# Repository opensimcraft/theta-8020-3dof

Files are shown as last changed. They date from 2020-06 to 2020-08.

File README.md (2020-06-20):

# SC230 Theta 3DOF Sim Rig
The SC230 Theta is a 3DOF sim rig made from 80/20 T-slot aluminum extrusions and
other components.

## Assemblies
The SC230 Theta is made up of several chassis that come together to create
the whole rig. The rig may be expanded by starting with the inner-most
cockpit and adding additional chassis to add motion later on.

* Cockpit Chassis
* Pitch/Yaw Chassis
* Roll Chassis
* Cradle Chassis
  * Note: The Cradle Chassis is required to suspend the Roll Chassis

## TODOs
The primary activity right now is to finalize the Cockpit Chassis as a 1.0
release of the project by itself.

* Convert the single Word assembly instructions document into individual
  assembly instructions for each chassis
* Verify the 80/20 part numbers and machine codes to produce the BOMs for each
  chassis
* Convert the SKP to STEP for use with FreeCAD and break into files for each
  chassis

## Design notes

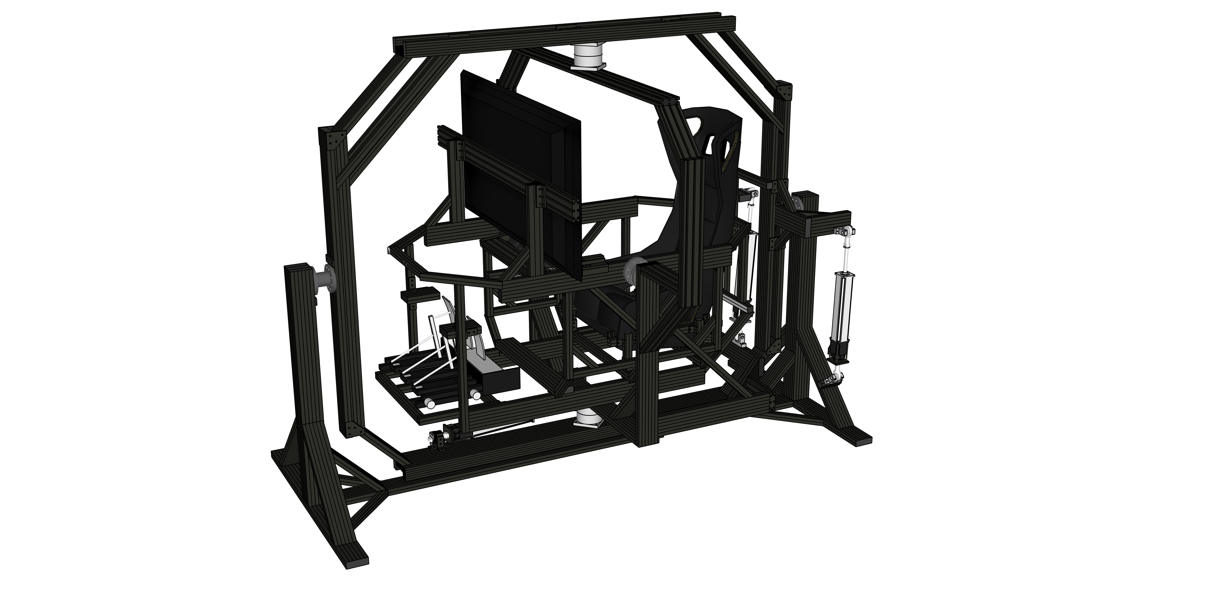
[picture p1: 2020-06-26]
SC230 Theta Large Screen.png

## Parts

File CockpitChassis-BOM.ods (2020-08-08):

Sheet: Export BOM
Open Sim Craft Part # | DIYSim Part # | Tag | Part # | Qty | Length Each (or area) | Units | 80/20 Description Note:all extrusion dimensions start at the left end
E9230301 | 9230301 | A | 1030-S | 2 | 38.25 | IN | 7036 Left; 7036 Right
 |  |  | 7003 | 2 |  | EA
 |  |  | 7036 | 2 |  | EA
E9230303 | 9230303 | B | 1010-S | 2 | 22 | IN | 7051 in S @ .500" Left; 7051 in S @ 1.500" Left; 7051 in S @ 2.500" Left, 7061 in Right
 |  |  | 7005 | 2 |  | EA
 |  |  | 7051 | 6 |  | EA
 |  |  | 7061 | 2 |  | EA
E9230906 | 9230906 | AB | 1010-S | 2 | 17 | IN | 7061 in Left; 7061 in Right, 7051 in S Left @ 2.250", 7051 in S Left @ 10.375"
 |  |  | 7005 | 2 |  | EA | 1
 |  |  | 7061 | 4 |  | EA | 1
 |  |  | 7051 | 4 |  | EA | 1
 |  |  | 7005 | 2 |  | EA | 1
 |  |  | 7051 | 6 |  | EA | 1
 |  |  | 7061 | 2 |  | EA | 1
E9230309 | 9230309 | C | 1010-S | 2 | 21.75 | IN | 7061 in Left; 7061 in Right
 |  |  | 7005 | 2 |  | EA | 1
 |  |  | 7061 | 4 |  | EA | 1
E9230310 | 9230310 | D | 1010-S | 2 | 10.85 | IN | 7061 in Left and Right, 7051 in S @ 0.500
 |  |  | 7005 | 2 |  | EA | 1
 |  |  | 7061 | 4 |  | EA | 1
 |  |  | 7051 | 2 |  | EA | 1
E9230312 | 9230312 | E | 1010-S | 2 | 19 | IN | 1010-S
 |  |  | 7005 | 2 |  | EA | 1
E9230313 | 9230313 | F | 1010-S | 6 | 13 | IN | 7042 in C Left; 7042 in A Left; 7061 in Right, 7051 in A Right @ 0.5"
 |  |  | 7005 | 6 |  | EA | 1
 |  |  | 7042 | 12 |  | EA | 1
 |  |  | 7061 | 6 |  | EA | 1
 |  |  | 7051 | 6 |  | EA | 1
E9230314 | 9230314 | G | 1010-S | 2 | 11 | IN | 7061 in Left; 7061 in Right, 7051 in S @ 0.500"
 |  |  | 7005 | 2 |  | EA | 1
 |  |  | 7061 | 4 |  | EA | 1
 |  |  | 7051 | 2 |  | EA | 1
E9230315 | 9230315 | H | 1010-S | 1 | 13 | IN | 1010-S
 |  |  | 7005 | 1 |  | EA | 1
E9230316 | 9230316 | I | 1020-S | 1 | 6.5 | IN | 1020-S
 |  |  | 7000 | 1 |  | EA | 1
E9230317 | 9230317 | J | 1010-S | 1 | 15 | IN | 7051 in S @ 7.000"; 7051 in S @ 8.000"
 |  |  | 7005 | 1 |  | EA | 1
 |  |  | 7051 | 2 |  | EA | 1
E9230318 | 9230318 | K | 1030-S | 2 | 36 | IN | 7036 Left; 7036 Right, 7050 in U @ 1.000" (U Channel adjacent to taps)
 |  |  | 7003 | 2 |  | EA | 1
 |  |  | 7036 | 4 |  | EA | 1
 |  |  | 7050 | 2 |  | EA | 1
E9230323 | 9230323 | L | 1010-S | 2 | 12 | IN | 7081; 7050 in slot R at 2.0" from Left End
 |  |  | 7005 | 2 |  | EA | 1
 |  |  | 7081 | 2 |  | EA | 1
 |  |  | 7050 | 2 |  | EA | 1
E9230324 | 9230323 | M | 1010-S | 2 | 12 | IN | 7081; 7050 in slot R at 5.0" from Left End
 |  |  | 7005 | 2 |  | EA | 1
 |  |  | 7081 | 2 |  | EA | 1
 |  |  | 7050 | 2 |  | EA | 1
E9230325 | 9230325 | N | 1010-S | 1 | 13 | IN | 7061 in Left; 7061 in Right; 7051 in S @ 2.000"; 7051 in S @ 3.000"; 7051 in S @ 10.000" ; 7051 in S @ 11.000" from left, 7253 in S @ 6.000"; 7253 in S @ 7.000" from left
 |  |  | 7005 | 1 |  | EA | 1
 |  |  | 7061 | 2 |  | EA | 1
 |  |  | 7051 | 4 |  | EA | 1
 |  |  | 7253 | 2 |  | EA | 1
E9230326 | 9230326 | O | 1030-S | 2 | 12 | IN | 7036 Left; 7036 Right
 |  |  | 7003 | 2 |  | EA | 1
 |  |  | 7036 | 4 |  | EA | 1
E9230327 | 9230327 | P | 1010-S | 1 | 22 | IN | 7051 in S @ 10.000"; 7051 in S @ 11.000"; 7051 in S @ 12.000"
 |  |  | 7005 | 1 |  | EA | 1
 |  |  | 7051 | 3 |  | EA | 1
E9230331 | 9230331 | Q | 1010-S | 2 | 5 | IN | 7051 in S @ 2.000";7051 in S @ 3.000"; 7051 in S @ 4.000"
 |  |  | 7005 | 2 |  | EA | 1
 |  |  | 7051 | 6 |  | EA | 1
E9230332 | 9230332 | R | 1010-S | 1 | 21 | IN | 7051 in S @ 2.500"; 7051 in R @ 9.500"; 7051 in R @ 10.500"; 7051 in R @ 11.500", 7051 in S @ 18.500"
 |  |  | 7005 | 1 |  | EA | 1
 |  |  | 7051 | 5 |  | EA | 1
E9230333 | 9230333 | S | 1010-S | 1 | 13 | IN | 7061 in Left; 7061 in Right, 7253 in S @ 5.500";7253 in S @ 6.500"; 7253 in S @7.500" from left
 |  |  | 7005 | 1 |  | EA | 1
 |  |  | 7061 | 2 |  | EA | 1
 |  |  | 7253 | 3 |  | EA | 1
E9230334 | 9230334 | T | 1030-S | 2 | 23 | IN | 7036 in Left; 7036 in Right
 |  |  | 7003 | 2 |  | EA | 1
 |  |  | 7036 | 4 |  | EA | 1
E9230335 | 9230335 | U | 1010-S | 2 | 8 | IN | 7051 in R Left @ 0.5"; 7051 in R Left @ 1.5";7051 in R Left @ 2.5";7051 in R Left @ 7.5"; 7051 in R Left @ 6.5"; 7051 in R Left @ 5.5"
 |  |  | 7005 | 2 |  | EA | 1
 |  |  | 7051 | 12 |  | EA | 1
E9230336 | 9230336 | V | 1020-S | 4 | 4 | IN | 1020-S
 |  |  | 7000 | 4 |  | EA | 1
E9230337 | 9230337 | W | 1030-S | 2 | 9.5 | IN | 7036 in Left; 7086 Right
 |  |  | 7003 | 2 |  | EA | 1
 |  |  | 7036 | 2 |  | EA | 1
 |  |  | 7086 | 2 |  | EA | 1
E9230338 | 9230338 | X | 1030-S | 2 | 18.5 | IN | 7086 Right
 |  |  | 7003 | 2 |  | EA | 1
 |  |  | 7086 | 2 |  | EA | 1
E9230339 | 9230339 | Y | 1030-S | 1 | 48 | IN | 7051 in V Left @ 0.5"; 7051 in VV Left @ 0.5"; 7051 in U Left @ 0.5"; 7051 in V Right @ 0.5"; 7051 in VV Right @ 0.5"; 7051 in U Right @ 0.5";
 |  |  | 7003 | 1 |  | EA | 1
 |  |  | 7051 | 6 |  | EA | 1
E9230340 | 9230340 | Z | 1020-S | 2 | 15 | IN | 7042 in E Left; 7042 in H Left; 7051 in T Right @ 0.5"; 7051 in T Right @ 1.5"
 |  |  | 7000 | 2 |  | EA | 1
 |  |  | 7042 | 4 |  | EA | 1
 |  |  | 7051 | 4 |  | EA | 1
E9230341 | 9230341 | AA | 1020-S | 2 | 11 | IN | 1020-S
 |  |  | 7000 | 2 |  | EA | 1
E9230906 | 9230906 | AB | 1010-S | 2 | 17 | IN | 7061 in Left; 7061 in Right, 7051 in S Left @ 2.250", 7051 in S Left @ 10.375"
 |  |  | 7005 | 2 |  | EA | 1
 |  |  | 7061 | 4 |  | EA | 1
 |  |  | 7051 | 4 |  | EA | 1
E9230907 | 9230907 | AC | 1010-S | 2 | 10 | IN | 7061 in Left; 7061 in Right, 7051 in S @ 4.250"
 |  |  | 7005 | 2 |  | EA | 1
 |  |  | 7061 | 4 |  |  | 1
 |  |  | 7051 | 2 |  |  | 1
E9230908 | 9230908 | AD | 1010-S | 2 | 12 | IN | 7061 in Left, 7051 in S @ .500", 7051 in S @ 11.500"
 |  |  | 7005 | 2 |  | EA | 1
 |  |  | 7061 | 2 |  | EA | 1
 |  |  | 7051 | 4 |  | EA | 1
E9230909 | 9230909 | AE | 1020-S | 2 | 5 | IN | 1020-S
 |  |  | 7005 | 2 |  | EA | 1
E9232565 | 9232565 | AF | 2565 | 14 |  | EA | 1
E9232570 | 9232570 | AG | 2570 | 8 |  | EA | 1
F9236850 | 9236850 | AH | 6850 | 2 |  | EA | 1
E9230319 | 9230309F | AI | 1030-S | 1 | 21.75 | IN | 7061 in Left; 7061 in Right, one hole on each side, same channel
 |  |  | 7003 | 1 |  | EA | 1
 |  |  | 7061 | 2 |  | EA | 1
E9230320 | 9230311a | AJ | 1010-S | 4 | 6 | IN | 7066 @ 45 degrees in Left w/ 7083 Counterbore
 |  |  | 7005 | 4 |  | EA | 1
 |  |  | 7066 | 4 |  | EA | 1
 |  |  | 7083 | 4 |  | EA | 1
E9230321 | 9230311b | AK | 1010-S | 4 | 6 | IN | 1010-S
 |  |  | 7005 | 4 |  | EA | 1
E9230322 | 9230314B | AL | 1010-S | 2 | 11 | IN | 7042 in C Left; 7042 in A Left; 7061 in Right
 |  |  | 7005 | 2 |  | EA | 1
 |  |  | 7042 | 4 |  | EA | 1
 |  |  | 7061 | 2 |  | EA | 1
F9234119 | 9234119 | AM | 4119 | 34 |  | EA | 10 Series 2 Hole - Inside Corner Bracket
F9234176 | 9234176 | AN | 4176 | 16 |  | EA | 10 Series 3 Hole - Inside Corner Bracket
F9234136 | 9234136 | AO | 4136 | 2 |  | EA | 10 Series 4 Hole - Tall Gusseted Inside Corner Bracket
F9234015 | 9234015 | AP | 4015 | 11 |  | EA | 10 Series 6 Hole - Wide 3x3 Inside Corner Bracket
F9234166 | 9234166 | AQ | 4166 | 4 |  | EA | 10 Series 6 Hole - Rectangular Flat Plate
F9234118 | 9234118 | AR | 4118 | 8 |  | EA | 10 Series 3 Hole - Straight Flat Plate
F9234107 | 9234107 | AS | 4107 | 2 |  | EA | 10 Series 2 Hole - Straight Flat Plate
F9233393 | 9233393 |  | 3393 | 200 |  | EA | Bolt Assembly: 1/4-20 x .500" Black BHSCS and Slide-In Economy T-Nut - Centered Thread - Black Zinc
F9233381 | 9233381 |  | 3381 | 36 |  | EA | Standard End Fastener, 1/4-20
F9233395 | 9233395 |  | 3395 | 20 |  | EA | 10 Series 10-32 Standard Anchor Fastener Assembly
F9234503 | 9234503 | AT | 4503 | 4 |  | EA | 10 to 15 Series 2 Hole - Transition Inside Corner Bracket
F9233321 | 9233321 |  | 3321 | 24 |  | EA | Bolt Assembly: 1/4-20 x .500" Black FBHSCS and Slide-In Economy T-Nut - Centered Thread - Black Zinc
F9233305 | 9233305 |  | 3305 | 16 |  | EA | Bolt Assembly: 1/4-20 x .875" Black SHCS and Slide-In Economy T-Nut - Centered Thread - Black Zinc
F9233307 | 9233307 |  | 3307 | 12 |  | EA | Bolt Assembly: 1/4-20 x 1.250" Black SHCS and Slide-In Economy T-Nut - Centered Thread - Black Zinc
F9233065 | 9233065 |  | 3065 | 12 |  | EA | 1/4-20 x .750" Button Head Socket Cap Screw (BHSCS)
F9233080 | 9233080 |  | 3080 | 12 |  | EA | 1/4-20 x 1.500" Socket Head Cap Screw (SHCS)
F9233258 | 9233258 |  | 3258 | 100 |  | EA | .286" ID Washer
F9233376 | 9233376 |  | 3376 | 24 |  | EA | 1/4-20 Roll-In T-Nut with Flex Handle
F9233416 | 9233416 |  | 3059 | 12 |  | EA | 1/4-20 x .375" Button Head Socket Cap Screw (BHSCS)
F9233416 | 9233416 |  | 3382 | 12 |  | EA | 1/4-20 Slide-in Economy T-Nut - Centered Thread
F9233822 | 9233822 |  | 3497 | 12 |  | EA | Bolt Assembly: 1/4-20 x .625" Black SHCS with Washer and Slide-In Economy T-Nut - Centered Thread - Black Zinc
F9233822 | 9233822 |  | 3497 | 24 |  | EA | Bolt Assembly: 1/4-20 x .625" Black SHCS with Washer and Slide-In Economy T-Nut - Centered Thread - Black Zinc
F9236416 | 9236416 | AU | 6416 | 2 |  | EA | 10 S 4" SINGLE FLANGE BEARINGBRAKE KIT READY
F9236540 | 9236540 |  | 11-6540 | 4 |  | EA | M6 X 40mm SHCS [BLACK]

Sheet: Bottom Mount Pedal Frame
Open Sim Craft Part # | DIYSim Part # | Tag | Part # | Qty | Length Each (or area) | Units | 80/20 Description Note:all extrusion dimensions start at the left end
E9230906 | 9230906 | AB | 1010-S | 2 | 17 | IN | 7061 in Left; 7061 in Right, 7051 in S Left @ 2.250", 7051 in S Left @ 10.375"
 |  |  | 7005 | 2 |  | EA | 1
 |  |  | 7061 | 4 |  | EA | 1
 |  |  | 7051 | 4 |  | EA | 1
F9233381 | 9233381 |  | 3381 | 8 |  | EA | Standard End Fastener, 1/4-20
E9230907 | 9230907 | AC | 1010-S | 2 | 10 | IN | 7061 in Left; 7061 in Right, 7051 in S @ 4.250"
 |  |  | 7005 | 2 |  | EA | 1
 |  |  | 7061 | 4 |  |  | 1
 |  |  | 7051 | 2 |  |  | 1
E9230908 | 9230908 | AD | 1010-S | 2 | 12 | IN | 7061 in Left, 7051 in S @ .500", 7051 in S @ 11.500"
 |  |  | 7005 | 2 |  | EA | 1
 |  |  | 7061 | 2 |  | EA | 1
 |  |  | 7051 | 4 |  | EA | 1

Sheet: Bottom Cockpit
Open Sim Craft Part # | DIYSim Part # | Tag | Part # | Qty | Length Each (or area) | Units | 80/20 Description Note:all extrusion dimensions start at the left end
E9230301 | 9230301 | A | 1030-S | 2 | 38.25 | IN | 7036 Left; 7036 Right
 |  |  | 7003 | 2 |  | EA
 |  |  | 7036 | 2 |  | EA
E9230303 | 9230303 | B | 1010-S | 2 | 22 | IN | 7051 in S @ .500" Left; 7051 in S @ 1.500" Left; 7051 in S @ 2.500" Left, 7061 in Right
 |  |  | 7005 | 2 |  | EA
 |  |  | 7051 | 6 |  | EA
 |  |  | 7061 | 2 |  | EA
F9234119 | 9234119 | AM | 4119 | 4 |  | EA | 10 Series 2 Hole - Inside Corner Bracket
F9234015 | 9234015 | AP | 4015 | 2 |  | EA | 10 Series 6 Hole - Wide 3x3 Inside Corner Bracket
E9230309 | 9230309 | C | 1010-S | 2 | 21.75 | IN | 7061 in Left; 7061 in Right
 |  |  | 7005 | 2 |  | EA
 |  |  | 7061 | 4 |  | EA
E9230319 | 9230309F | AI | 1030-S | 1 | 21.75 | IN | 7061 in Left; 7061 in Right, one hole on each side, same channel
 |  |  | 7003 | 1 |  | EA
 |  |  | 7061 | 2 |  | EA
E9232565 | 9232565 | AF | 2565 | 6 |  | EA

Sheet: Rear Cockpit
Open Sim Craft Part # | DIYSim Part # | Tag | Part # | Qty | Length Each (or area) | Units | 80/20 Description Note:all extrusion dimensions start at the left end
E9230332 | 9230332 | R | 1010-S | 1 | 21 | IN | 7051 in S @ 2.500"; 7051 in R @ 9.500"; 7051 in R @ 10.500"; 7051 in R @ 11.500", 7051 in S @ 18.500"
 |  |  | 7005 | 1 |  | EA
 |  |  | 7051 | 5 |  | EA
E9232570 | 9232570 | AG | 2570 | 2 |  | EA
E9230310 | 9230310 | D | 1010-S | 2 | 10.85 | IN | 7061 in Left and Right, 7051 in S @ 0.500
 |  |  | 7005 | 2 |  | EA
 |  |  | 7061 | 4 |  | EA
 |  |  | 7051 | 2 |  | EA

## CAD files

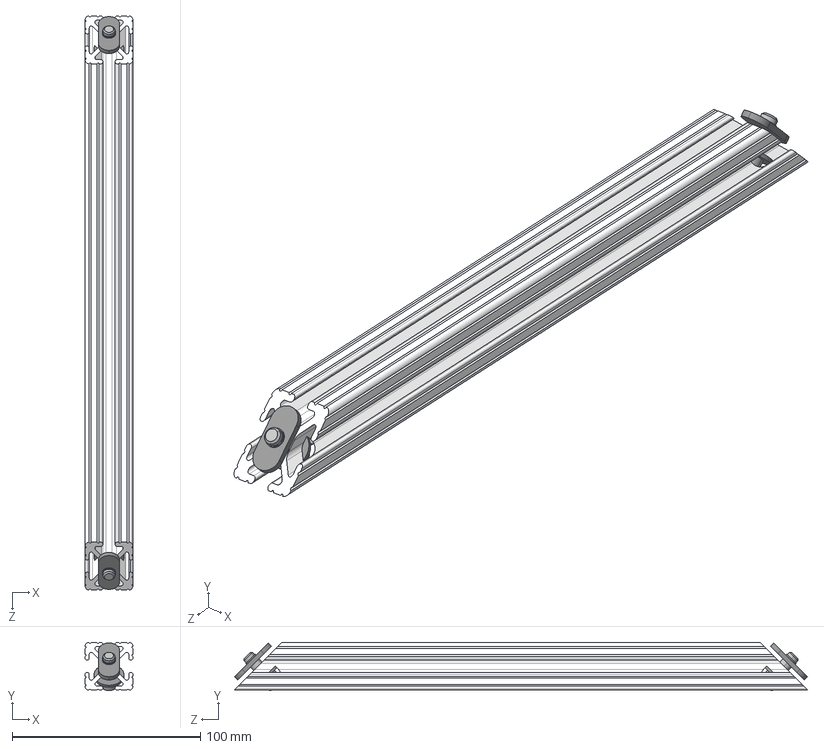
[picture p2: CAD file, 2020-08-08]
8020-stepfiles/8020-2570.STEP
25.4 x 25.6 x 304.8 mm
1010-12in
socket head cap screw_ai_HX-SHCS 0.25-20x0.625x0.625-N x 2

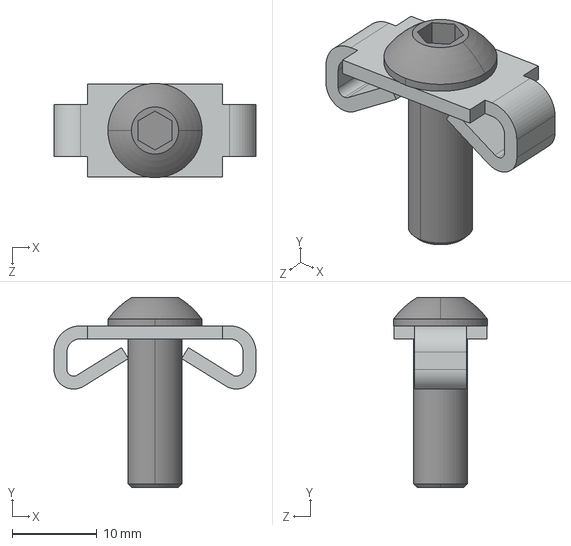
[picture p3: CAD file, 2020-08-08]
8020-stepfiles/8020-3381.STEP
23.8 x 22.4 x 11.1 mm
8020-3381-$PARTNUMBER_3378
8020-3381-$PARTNUMBER_3065

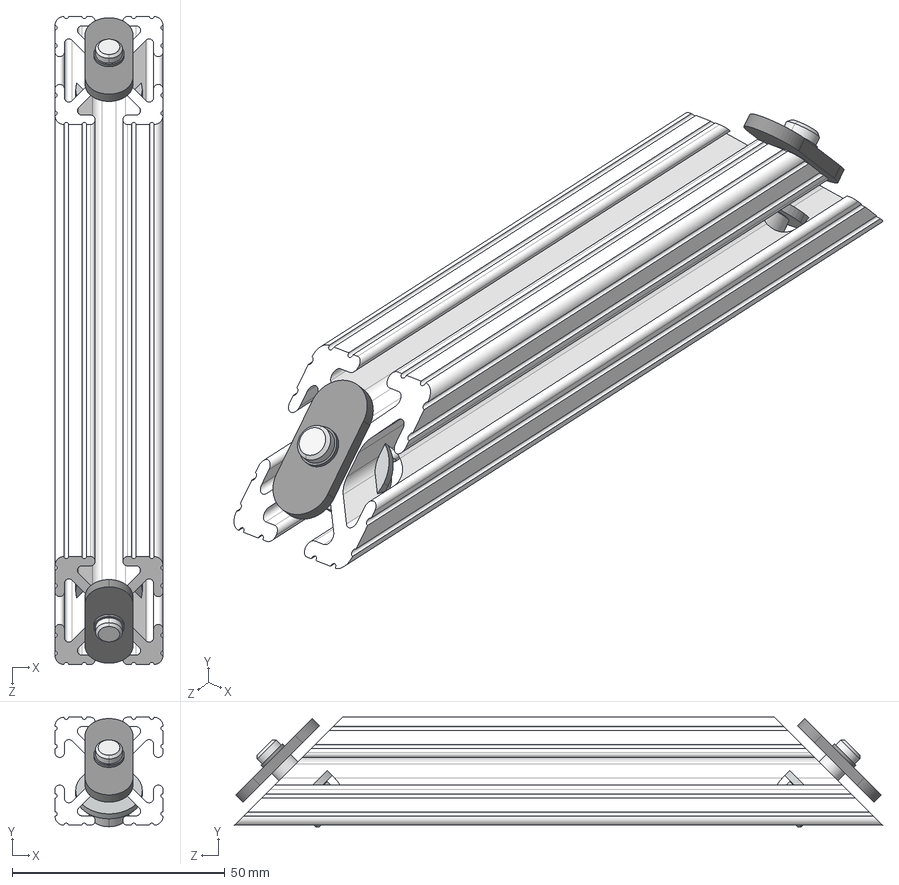
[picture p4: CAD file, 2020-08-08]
8020-stepfiles/8020-2565.STEP
25.4 x 25.8 x 152.4 mm
3258_Preferred Wide FW 0.25 x 2

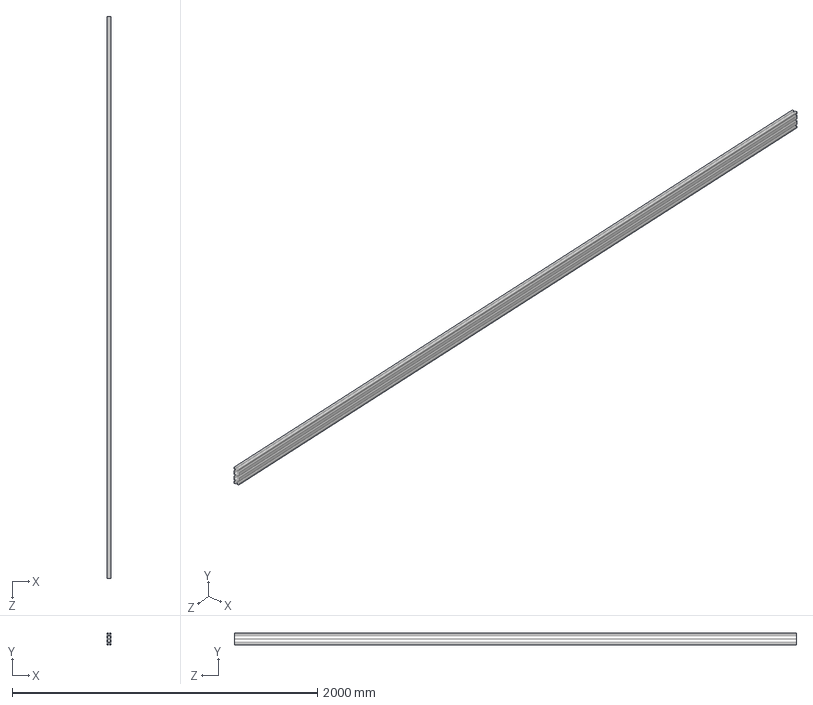
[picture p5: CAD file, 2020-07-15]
8020-stepfiles/8020-1030-S X 145.step
25.4 x 76.2 x 3683.0 mm

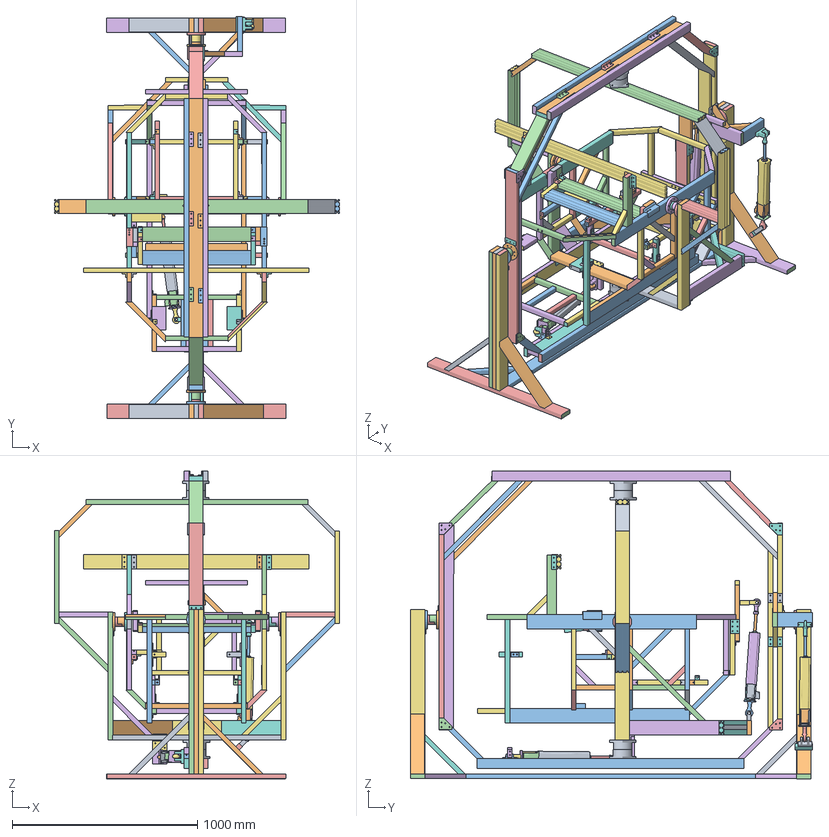
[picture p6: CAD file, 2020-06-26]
sc230_theta_large_screen-from-dae.FCStd
1539.5 x 2171.3 x 1661.5 mm

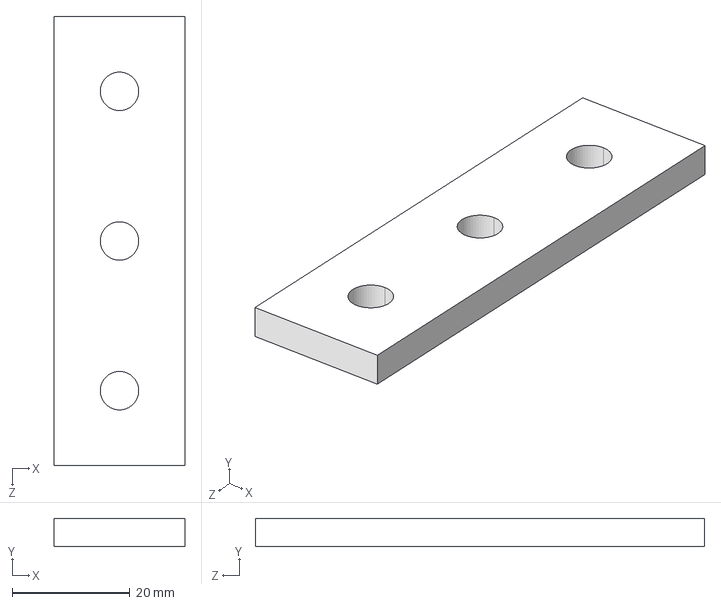
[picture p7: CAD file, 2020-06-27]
8020-stepfiles/8020-4118.step
22.2 x 4.78 x 76.2 mm

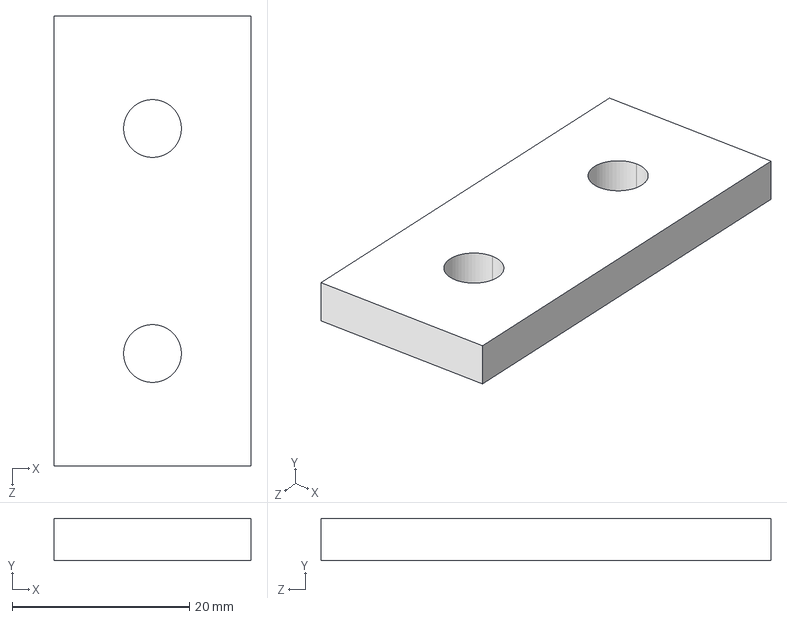
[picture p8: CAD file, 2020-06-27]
8020-stepfiles/8020-4107.step
22.2 x 4.78 x 50.8 mm

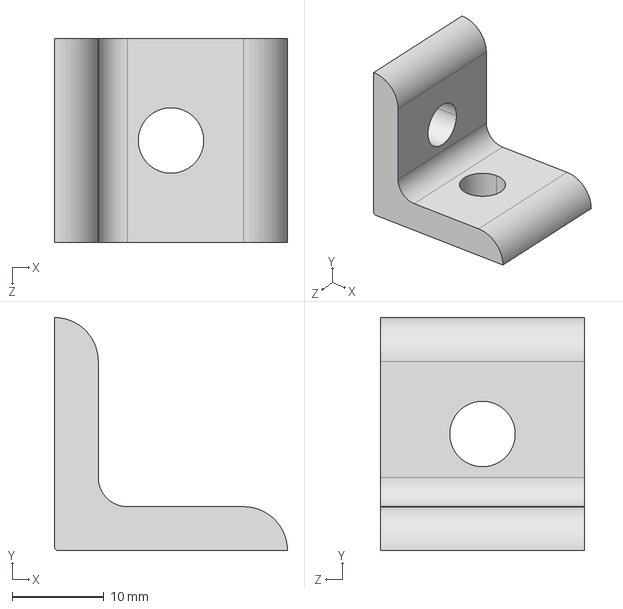
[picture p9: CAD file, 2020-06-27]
8020-stepfiles/8020-4119.step
25.4 x 25.4 x 22.2 mm

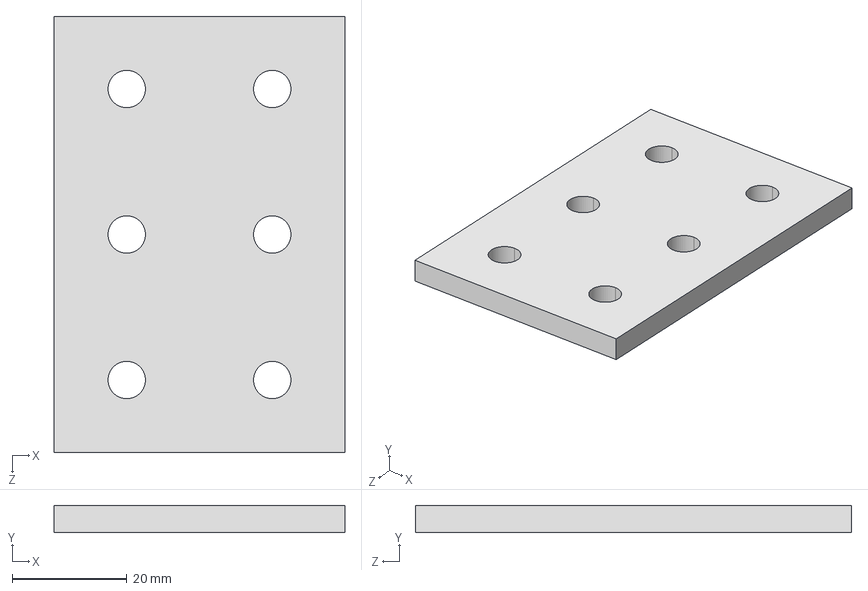
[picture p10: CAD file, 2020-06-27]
8020-stepfiles/8020-4166.step
50.8 x 4.78 x 76.2 mm

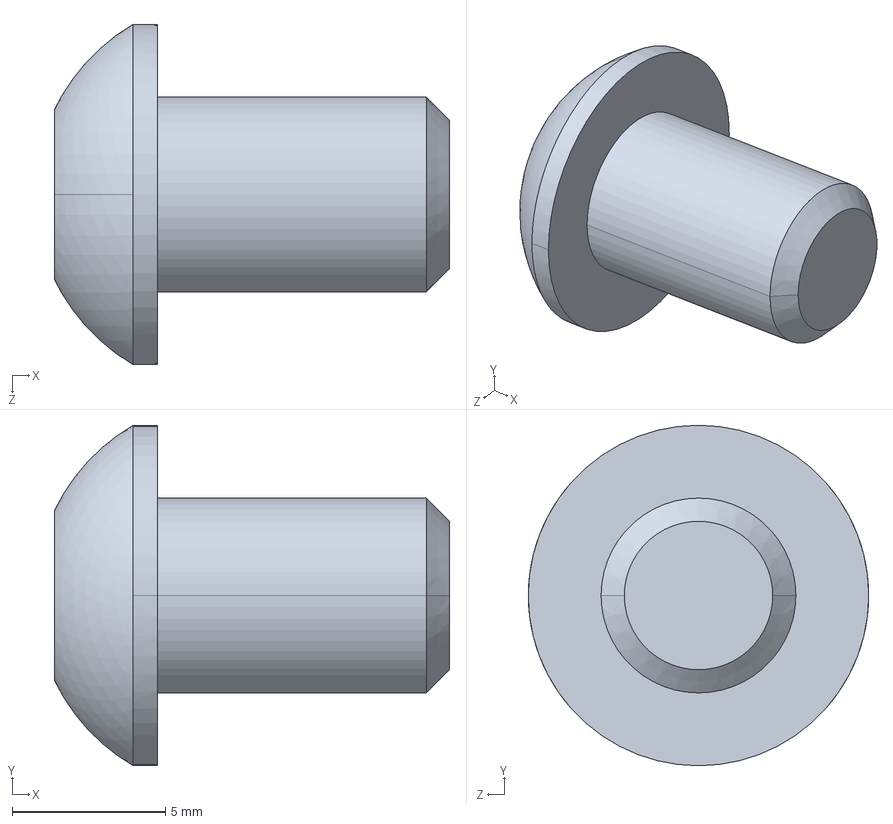
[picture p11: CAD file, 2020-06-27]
8020-stepfiles/8020-3059.step
12.9 x 11.1 x 11.1 mm

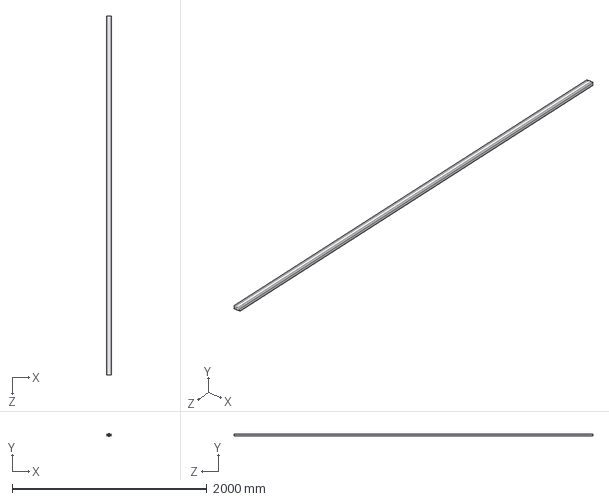
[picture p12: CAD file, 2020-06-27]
8020-stepfiles/8020-1020-S X 145.step
50.8 x 25.4 x 3683.0 mm

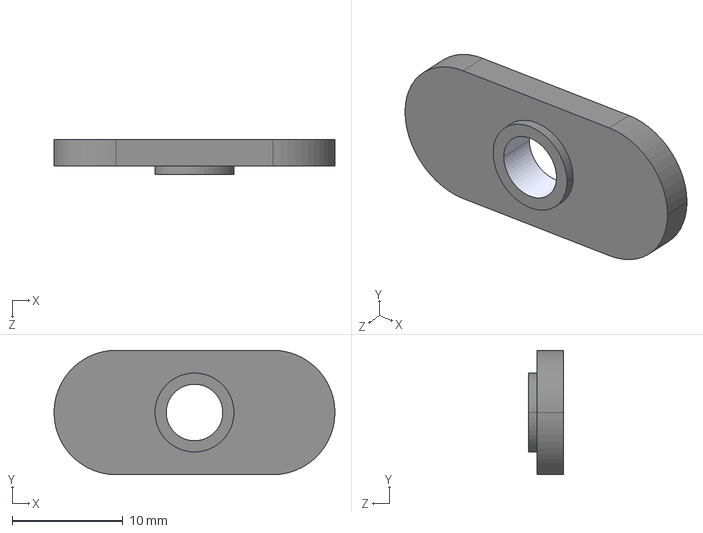
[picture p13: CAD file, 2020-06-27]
8020-stepfiles/8020-3382.step
25.4 x 11.3 x 3.17 mm

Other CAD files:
bottom-mount-pedal-frame/Subassembly_Bottom_Mount_Pedal_Frame.FCStd
cockpit-rear/Subassembly_Cockpit_Rear.FCStd
cockpit-bottom/Subassembly_Cockpit_Bottom.FCStd
extrusion-profile-1010-S.FCStd
extrusion-profile-1020-S.FCStd
extrusion-profile-1030-S.FCStd
8020-stepfiles/8020-1010-S X 145.step
8020-stepfiles/8020-3065.step
8020-stepfiles/8020-3080.step
8020-stepfiles/8020-3258.step
8020-stepfiles/8020-4015.step
8020-stepfiles/8020-4136.step
8020-stepfiles/8020-4176.step
8020-stepfiles/8020-4503.step
bottom-mount-pedal-frame/E9230906.FCStd
bottom-mount-pedal-frame/E9230907.FCStd
bottom-mount-pedal-frame/E9230908.FCStd
cockpit-bottom/E9230301.FCStd
cockpit-bottom/E9230303.FCStd
cockpit-bottom/E9230309.FCStd
cockpit-bottom/E9230319.FCStd
cockpit-bottom/E9232565.FCStd
cockpit-rear/E9230310.FCStd
cockpit-rear/E9230332.FCStd
cockpit-rear/E9232570.FCStd
fasteners-brackets-etc/F9234015.FCStd
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

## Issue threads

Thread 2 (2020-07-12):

machine codes in bottom mount pedal assembly need to be rectified

thoraxe, 2020-07-12:
Looking at the sample equipment I received from SimCraft, it appears that the machine codes for 9230906 are not entirely correct.

> There are 3-7051. The one at 2.250”, the one at 10.375”, but also one at 6.375”. This doesn’t match the CAD in terms of the spacing between the components.

This is also added as a comment on the BOM tab where the pedal mount assembly appears.

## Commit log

2020-06-20 adds distinct cockpit chassis documentation
2020-06-23 Add files via upload
    Stepfile Added
    [sc230_LargeScreen v1.step]
2020-06-26 adds freecad file
    [sc230_theta_large_screen.FCStd]
2020-06-26 removes empty step file
    [sc230_LargeScreen v1.step]
2020-06-27 adds step files for various 8020 components
    [8020-1010-S X 145.step, 8020-1020-S X 145.step, 8020-3059.step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]
2020-06-29 adds BOM spreadsheet for cockpit chassis
    [CockpitChassis-BOM.ods]
2020-07-11 Adds a sheet for the bottom pedal frame
    This adds a sheet which has a BOM specific for the bottom pedal frame. We may
    or may not make multiple sheets for each of the sub-assemblies that go into the
    main assemblies.
    [CockpitChassis-BOM.ods]
2020-07-11 Adds bottom mount pedal frame files
    [9230906.FCStd, 9230907.FCStd, 9230908.FCStd]
2020-07-12 Adds assembly files for Assembly4
    This creates individual assemblies from the previously added parts and then
    creates a parent assembly for the bottom frame.
    [9230906-assy.FCStd, 9230907-assy.FCStd, 9230908-assy.FCStd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]
2020-07-12 adds BOM comment about discrepancy in machine codes
    [CockpitChassis-BOM.ods]
2020-07-15 adds remaining extrusions to bottom mount pedal frame assembly
    [9230908-assy.FCStd, bottom-mount-pedal-frame-assy.FCStd]
2020-07-15 adds 1030-s step file
    [8020-1030-S X 145.step]
2020-07-15 Starts to work on base cockpit
    * This adds a simple extrusion profile from which to make other 1010-S parts.
    * It adds a folder to store converted parts/assemblies for fasteners, brackets,
    etc.
    * It adds the starting parts for the base cockpit frame
    [1010-S-extrusion-profile.FCStd, 9230301-assy.FCStd, 9230301.FCStd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]
2020-07-15 starting to break out base cockpit BOM
    [CockpitChassis-BOM.ods]
2020-07-25 New parts scheme and practicing Assembly4
    * Fixes up BOM with new part numbering scheme
    * Adds and renames extrusion profiles to work with FreeCAD naming (can't
    start with a number
    * Creates a LibreOffice document version of the assembly instructions
    * Complete redo of the bottom mount pedal frame's individual parts
    * New subassembly / assembly4 file for the bottom mount pedal frame
    [1010-S-extrusion-profile.FCStd, 9230906-assy.FCStd, 9230906.FCStd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]
2020-08-01 Restarts base cockpit frame using new part scheme
    * adds new fasteners with LCS in holes
    * recreates some extrusions for base cockpit
    * gets rid of some old things
    * fixes some BOM issues
    [9230301-assy.FCStd, 9230301.FCStd, 9230303-assy.FCStd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]
2020-08-08 Several big changes to subassemblies
    * moves base-cockpit-frame to cockpit-bottom
    * starts on cockpit rear
    * creates supporting parts
    * adds several step files that are sources
    * updates BOM accordingly
    [8020-2565.STEP, 8020-2570.STEP, 8020-3381.STEP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]
